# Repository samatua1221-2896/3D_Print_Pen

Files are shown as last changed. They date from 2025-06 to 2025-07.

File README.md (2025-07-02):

# 3D_Print_Pen

This is a fully custom 3D print pen that is able to use standard 1.75 filament and work with temperatures of 130°C to 240°C

fullModel

## Features

- Uses an Arduino Nano to control heating and motor functions
- Temperature dial lets you adjust the nozzle from 130 °C to 240 °C
- PID-controlled heater ensures smooth, stable temperature during use
- 12V 40W MK8-style heater cartridge melts standard 1.75 mm filament
- Compact custom PCB designed in KiCad
- Extrude button: hold to feed, double-tap for continuous release, tap again to stop
- Retract button: same controls in reverse for removing filament
- Motor direction and latching fully handled in firmware with debounce and timing
- Heater auto-shuts off if temp exceeds 260 °C or if thermistor fails
- Failsafe defaults ensure motor and heater are off on startup or error

## Details

This was pretty much my first full dive into a full blast of hardware and software combined in my own project that I'm making from scratch. I got inspiration from the MYNT3D style pen that I had but had been dealt some damage with wear and tear over the years so I decided to try and make my own. Overall, this was a pretty fun project where I was able to get a much better understand of KiCad and Onshape which is definitely going to help me for future projects that I'll be working on. A 3D print pen is also pretty close to a 3D printer that I'm hoping to get but if all else fails I'll have a pretty cool piece of hardware that I'll know I completely designed from scratch.

## Photos

Front & Back Exploded Views

frontExplodedView
backExplodedView

Pictures of PCB Board Front & Back

frontPrintPenPCB
backPrintPenPCB

Schematic Wiring

printPenSchematic

## Assembly Instructions

Most of this is a pretty straightforward setup with the PCB board being the main center of the pen that has all of the THT components sticking out of the case in order or operation to happen. If it is not defined inside of the 3D model how something is secured, the object is glued to the nearest surrounding case area. For example, the hotend nozzle will be glued to the innermost cylinder in order to minimize the amount of screws and scructural instability inside of the case itself.

## Side Notes

I do understand the preference of getting supplies from places like AliExpress, but unfortunately, living in Hawaii removes a lot of the options that are even availble on such websites. The best option for getting things to Hawaii in time for the Highway event is unfortunately going to need increased shipping. (Just for context, the PCB I ordered at the beginning on June still hasn't arrived yet) That means that some items in my BOM are a little pricier that AliExpress or otherwise counterparts but they are guaranteed able to arrive on time for the end of the event.

## Bill Of Materials

| Item |  Quantity | Price | Link |
|---|---|---|---|
| Arduino Nano | 3 | $7.99 | https://www.amazon.com/YELUFT-ATmega328P-Microcontroller-Mini-USB/dp/B0DWMQVCRF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 |
| IRLZ44N MOSFET | 1 | $1.30 | https://www.digikey.com/en/products/detail/infineon-technologies/IRLZ44NPBF/811808 |
| L293D Motor Driver IC | 1 | $7.85 | https://www.digikey.com/en/products/detail/stmicroelectronics/L293D/634700 |
| 10K Potentiometer (Vertical Mount) | 1 | $0.78 | https://www.digikey.com/en/products/detail/amphenol-piher-sensing-systems/PT10WV10-103A2020-3-NE-S/13244529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 |
| MK8 Hotend Heating Kit | 1 | $17.35 | https://www.amazon.com/KITQLPG-Assembled-Extruder-Aluminum-Creality/dp/B0DM1XC4MV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 |
| 12V 2A Power Adapter | 1 | $0.00 | N/A |
| 220 Ohm Resistor | 1 | $0.10 | https://www.digikey.com/en/products/detail/vishay-beyschlag-draloric-bc-components/MBA02040C2203FRP00/336479 |
| 10K Ohm Resistor | 2 | $0.20 | https://www.digikey.com/en/products/detail/stackpole-electronics-inc/RNF14FTD1K00/1706678 |
| 100uF 16V Electrolytic Capacitor | 2 | $0.24 | https://www.digikey.com/en/products/detail/w%C3%BCrth-elektronik/860020372006/5727030 |
| 0.1uF Ceramic Capacitor | 2 | $0.44 | https://www.digikey.com/en/products/detail/kemet/C320C104K5R5TA/818040 |
| 100K NTC Thermsistor EPCOS | 1 | $0.82 | https://www.digikey.com/en/products/detail/epcos-tdk-electronics/B57891M0104J000/739908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 |
| Mini DC Motor 12 V | 1 | $7.31 | https://www.amazon.com/Motor-DC12V-11RPM-Right-Printing/dp/B0B82JPGRB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 |
| Terminal Block 2-pin 3.5mm | 2 | $0.72 | https://www.digikey.com/en/products/detail/w%C3%BCrth-elektronik/691137710002/6644051 |
| Pin Header 1x2 2.54 | 1 | $0.10 | https://www.digikey.com/en/products/detail/harwin-inc/M20-9990246/3728226 |
| M3 Screws | 12 | $5.89 | https://www.digikey.com/en/products/detail/apm-hexseal/RM3X10MM-2701/3712296 |
| 18 AWG Wire | 1 | $6.99 | https://www.amazon.com/Automotive-Flexible-Security-Stranded-Electrical/dp/B0CKR35SX5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 |
| 22 AWG Wire | 1 | $8.98 | https://www.amazon.com/Electrical-Gauge-Silicone-Cable-Black/dp/B0746HG158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 |
| Buttons | 2 | $2.74 | https://www.digikey.com/en/products/detail/c-k/D6C90-F2-LFS/1466345 |
| Shipping for DigiKey | 1 | $20.00 | N/A |
| Shipping for Printing Legion | 1 | $10.00 | N/A |
| DC Barrel Jack | 1 | $1.50 | https://www.digikey.com/en/products/detail/same-sky-formerly-cui-devices/PJ-202AH/408450 |
| PCB Board | 1 | $15.28 | JLCPCB  |
| | | | |
| Total Cost | | $119.32 | |

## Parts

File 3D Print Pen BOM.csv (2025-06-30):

Actual Item Name & Use | Quantity | Order | Cost | Notes | Link to Buy | Status | Order date
Arduino Nano | 3 | 1pcs Nano V3.0 Board with Cable ATmega328P MCU CH340G Chip 5V 16M Microcontroller Compatible with Arduino Nano (Soldered, Type-C Port) | $7.99 |  | https://www.amazon.com/YELUFT-ATmega328P-Microcontroller-Mini-USB/dp/B0DWMQVCRF?s=industrial | Approved
IRLZ44N MOSFET | 1 | IRLZ44NPBF | $1.30 |  | https://www.digikey.com/en/products/detail/infineon-technologies/IRLZ44NPBF/811808 | Approved
L293D Motor Driver IC | 1 | L293D | $7.85 |  | https://www.digikey.com/en/products/detail/stmicroelectronics/L293D/634700 | Approved
10K Potentiometer (Vertical Mount) | 1 | PT10WV10-103A2020-3-NE-S | $0.78 |  | https://www.digikey.com/en/products/detail/amphenol-piher-sensing-systems/PT10WV10-103A2020-3-NE-S/13244529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 | Approved
MK8 Hotend Heating Kit | 1 | 1 Pcs 3D Printer Part 12V 24V Assembled Extruder Hotend Kit MK8 Nozzle Aluminum Heat Block/Fit for Creality Ender-3/CR-10/CR-10 Pro(for CR10 Pro 24V) | $17.35 |  | https://www.amazon.com/KITQLPG-Assembled-Extruder-Aluminum-Creality/dp/B0DM1XC4MV?s=industrial | Approved
12V 2A Power Adapter | 1 | N/A | $0.00 | Already Own | N/A | Delivered
220 Ohm Resistor | 1 | MBA02040C2203FRP00 | $0.10 |  | https://www.digikey.com/en/products/detail/vishay-beyschlag-draloric-bc-components/MBA02040C2203FRP00/336479 | Approved
10K Resistor | 2 | RNF14FTD1K00 | $0.20 |  | https://www.digikey.com/en/products/detail/stackpole-electronics-inc/RNF14FTD1K00/1706678 | Approved
100µF 16V Electrolytic Capacitor | 2 | 860020372006 | $0.24 |  | https://www.digikey.com/en/products/detail/w%C3%BCrth-elektronik/860020372006/5727030 | Approved
0.1µF Ceramic Capacitor | 2 | C320C104K5R5TA | $0.44 |  | https://www.digikey.com/en/products/detail/kemet/C320C104K5R5TA/818040 | Approved
100K NTC Thermistor EPCOS | 1 | B57891M0104J000 | $0.82 |  | https://www.digikey.com/en/products/detail/epcos-tdk-electronics/B57891M0104J000/739908 | Approved
Mini DC Motor 6V-12V | 1 | Gear Motor, DC12V 11RPM N20 Right Angle Metal Micro Gear Motor Low Speed Low Noise Brush DC Motor for 3D Printing Pen | $7.31 |  | https://www.amazon.com/Motor-DC12V-11RPM-Right-Printing/dp/B0B82JPGRB?s=industrial | Approved
Terminal Block 2-pin 3.5mm | 2 | 691137710002 | $0.72 |  | https://www.digikey.com/en/products/detail/w%C3%BCrth-elektronik/691137710002/6644051 | Approved
Pin Header 1x2 2.54mm | 1 | M20-9990246 | $0.10 |  | https://www.digikey.com/en/products/detail/harwin-inc/M20-9990246/3728226 | Approved
M3 Screws | 12 | RM3X10MM 2701 | $5.89 |  | https://www.digikey.com/en/products/detail/apm-hexseal/RM3X10MM-2701/3712296 | Approved
18 AWG Wire | 1 | 18 Gauge Wire (2-Pack Red/Black Each 25 FT), 18 AWG Automotive Wire, CCA, Speaker Audio Cable, Flexible Low Voltage Security Alarm Hook Up Control Cable, Stranded Electrical Wires for DIY DC | $6.99 |  | https://www.amazon.com/Automotive-Flexible-Security-Stranded-Electrical/dp/B0CKR35SX5?s=industrial | Approved
22 AWG Wire | 1 | 22awg Silicone Electrical Wire Cable 6 Colors (10ft Each) 22 Gauge Hookup Wires kit Stranded Tinned Copper Wire Flexible and Soft | $8.98 |  | https://www.amazon.com/Electrical-Gauge-Silicone-Cable-Black/dp/B0746HG158?s=industrial | Approved
Buttons | 2 | D6C90 F2 LFS | $2.74 |  | https://www.digikey.com/en/products/detail/c-k/D6C90-F2-LFS/1466345 | Approved
Shipping for DigiKey | 1 | N/A | $20.00 |  | N/A | Approved
Shipping for PETG 3D Print Parts | 1 | N/A | $10.00 |  | N/A | Approved
DC Barrel Jack (Female, PCB Mount) | 1 | PJ-202AH | $1.50 |  | https://www.digikey.com/en/products/detail/same-sky-formerly-cui-devices/PJ-202AH/408450 | Approved
PCB | 1 | PCB | $15.28 | Projected Cost, May Increase w/ Shipping | JLCPCB
 |  |  | $119.32

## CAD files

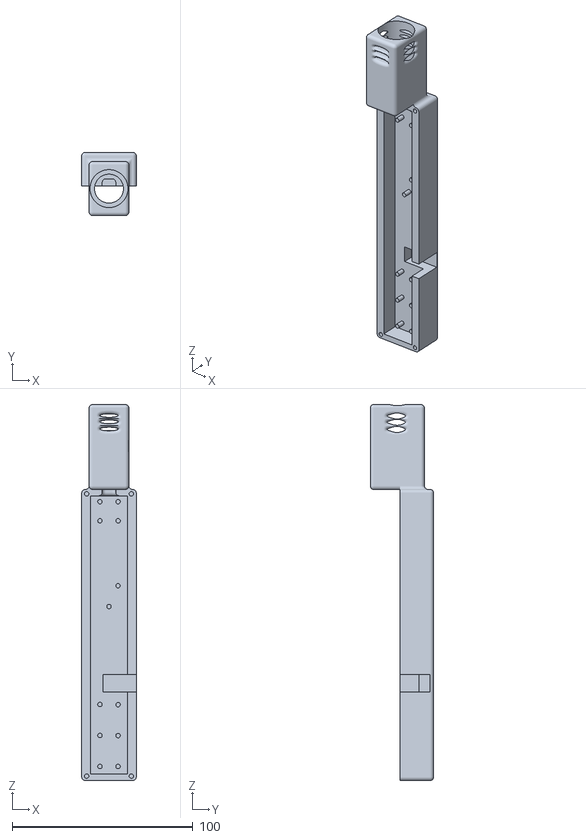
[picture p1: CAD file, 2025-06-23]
CAD/Main Case.stl
30.2 x 35.1 x 208.0

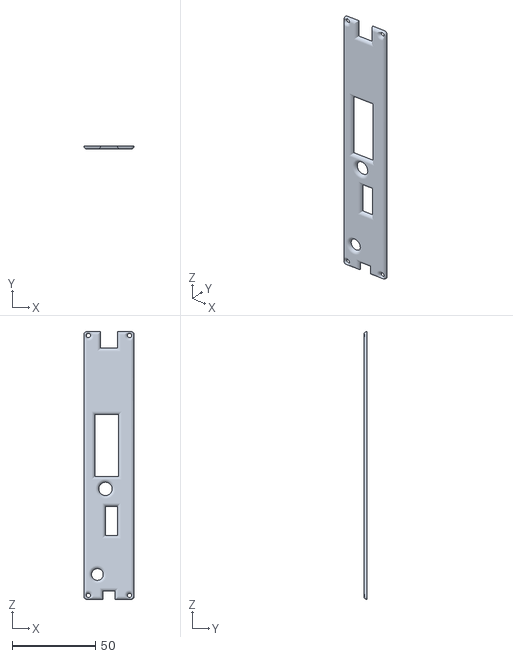
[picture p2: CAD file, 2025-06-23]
CAD/Top Case.stl
30.2 x 2.00 x 161.0

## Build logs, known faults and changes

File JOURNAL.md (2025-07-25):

| Title | Author | Description | Date Started |
| --- | --- | --- | ---|
| Arm Assistant | @samatua1221-2896 | A custom 3D printing pen | 6/18/25 |

### Overall Time Spent Designing as of July 1: 35 hrs

# June 18, 2025 (7 hours)

Today I decided I wanted to try and make a custom 3D printing pen that's pretty simple in terms of its ability but also has basic functionality. (I also really want some type of 3D printing tool like a 3D printer from highway maybe...) I started to base the concept off of MYNT3D's pen, it took me a little while but I was actually able to break it apart and figure out how the entire thing worked.

Based on the pictures below, I figured out that the pen had a potentiometer to adjust the temperature settings, there were two buttons to control the extruding and retraction of the filament, there was a slider to adjust the speed, and a small DC motor to actually control the movement of the filament. I decided I wanted to basically keep the basic functionality of the MYNT3D pen but have my own spin on it. I did want the entire thing to be powered by a 12V barrel jack to keep it simple. The microcontroller that was inside the MYNT pen looked to be some type of custom-made object, so I decided to use an Arduino Nano to keep it pretty simple for me so far.




So far I've been working on the schematic that I can use, I eventually settled on keeping the manual potentiometer instead of a LCD screen, aside from that, I've just been working to keep the whole thing pretty simple and not too complex in its parts, also using THT components cause I've never had experience working with surface mounted components. Below is the main schematic that I have so far for it.

Screenshot 2025-06-18 5 01 48 PM

Tomorrow I'll work on arranging the PCB and starting to work on the CAD and wiring structure for the pen.

# June 19, 2025 (8 hrs)

Today I worked on getting my BOM in order and finishing up the design of my PCB. So far, it's looking like theres not too much to do. I did start working on my BOM and figuring out how to get the products, I started using AliExpress and was extrememly happy to find that almost everything I needed was super cheap and not a problem to find at all. Then I went to go check out and found that none of them ship to Hawaii (:( whyyyy tarrifs) so it looks like I'm going to be searching on Amazon for the best prices again even if that means a little bit of a cost raise. 

Aside from that, now it looks like I've finished my PCB and it's not looking to bad if I say so myself. The pieces are relatively simple to fix and put on so I think it's looking pretty good so far.

Screenshot 2025-06-19 11 49 11 PM

I did spend quite a bit of time trying to fix all the rails, but pretty much I think this should be the final version of my PCB. Im planning on having the buttons on top and the power and potentiometer coming out of the back just to avoid having some things at awkward positions while I'm using the pen. 

# June 20, 2025 

I spend A LOT of time trying to finalize my BOM today so I can start working on the CAD to place everything. I did start with Amazon thinking I wouldn't be able to afford shipping from anywhere else when I happened to stumble on DigiKey! Thank god they're US based so there's not going to be too many charges aside from regular shipping to Hawaii. Majority of the parts that I'm going to need are just going to be soldered though-hole on my PCB since it's easier for my project. I am keeping some of the parts on Amazon just because I feel like those should be higher quality items that are vetted more for my project so hopefully that's ok. I did end up picking a nozzle from what an Ender 3D printer would be using because I didn't want my project to be your run-of-the-mill 3D pen, I did want to try and be a little more creative so I wanted to try and play around with that type of heat tip.

So far this is what I have in my BOM, it's pretty messy but I think I should be able to clean it up pretty nicely over the next two days. For me personally, I'm trying to finish this project BEFORE July so I can eventually get enough points for that 3D printer.

# June 21, 2025 (10 hrs - last 2 days)

I actually did end up having a much harder time dealing with the actual PCB design of the baord once I realized that my tracks were probabaly too thin for the amount of power that I was trying to use. After plenty of time trying to figure out how to asign net classes to all of my parts, I eventually was able to wire everything up and after even MORE time I was able to manuever all of my wiring around the thicker lines. 

Screenshot 2025-06-21 8 05 26 PM
Screenshot 2025-06-21 8 05 56 PM

I did stop my journal a little early yesterday because of one of my brother's basketball games, but I did end up figuring out all of my BOM materials. So far, it's looking like it'll be around $100, well under the grant limit for my project I hope (fingers crossed!) Listed below is my current BOM that hopefully wont change much more since I'll start working on the CAD now. Majority of my supplies are going to be sourced from Digikey with "higher quality" items coming from Amazon.

Screenshot 2025-06-21 8 35 13 PM

Now I'm going to start making mockups for the whole 3D pen in Onshape, hopefully it won't take too long.

# June 22, 2025 (5 hrs)

So that actually took a LOT longer than I thought it would take. I'm realizing now that a lot of the components are bigger than I previously thought they would be so I'm going to try and shift around the design a little bit to try and mae sure that I can keep what I have so far which is there below.

Screenshot 2025-06-22 1 20 25 AM

# June 28, 2025 (3 hrs)

It's been a while since I've been able to work on the project, but now it loks like that it should be wrapping up now. CAD is now I belive completely finished with so now I have a complete plan for where everything will go and how it will all work. I did have to change a couple of things due to the size of the nozzle. I was planning on having everything to do with the nozzle be wrapped inside of the case but I don't believe I'm skilled in CAD enough to know how to do it in a way that would protect the PCB and be physically stable. I did add a couple of things like ventilation holes on the side of the nozzle and shifted around the placement of the motor that will carry the filament. Aside from that, just minor things like smoothing out all the edges and making sure all my parts are the correct ones are pretty much all I have left for CAD. Soon I'll start on writing the code for it but it should be a pretty simple task.

Screenshot 2025-06-28 7 53 55 PM
Screenshot 2025-06-28 7 54 03 PM
Screenshot 2025-06-28 7 45 57 PM

Ok, I just finished writing up the code with a good amount of help from ChatGPT since I'm not super experienced in it but I do believe that I am now finished and now I'm going to be working on the README and the submission files, crossing fingers for a good result!

# July 1, 2025 (2 hrs)

Today I really just spent time working on the README file and doing the finishing touches on all of my CAD files and labeling. Hopefully the project looks good and I'm going on the submission now, so wish me luck!

# July 24, 2025

Finally got my grant and some of the parts started to arrive today, going to wait until tomorrow to start soldering everything together so I can get the rest of my packages coming from Amazon.

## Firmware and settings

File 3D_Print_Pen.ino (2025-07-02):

/* -----------------------------------------------------------------
   DIY 3‑D Printing Pen – Full Firmware
   Hardware (per KiCad project):
     * Arduino Nano V3 / Nano Every
     * L293D (IN1 = D2, IN2 = D3, EN1/2 tied HIGH or PWM for speed)
     * IRLZ44N MOSFET gate on D9  (Heater PWM)
     * Extrude button  on D4   (to GND, INPUT_PULLUP)
     * Retract button  on D5   (to GND, INPUT_PULLUP)
     * Potentiometer   on A1   (10 kΩ, sets 130‑240 °C)
     * Thermistor      on A0   (100 kΩ NTC, β ~ 3950, 10 kΩ pull‑up to 5 V)
------------------------------------------------------------------- */

#include <Arduino.h>

/* ---------- PIN DEFINITIONS ---------- */
constexpr uint8_t PIN_IN1       = 2;    // L293D IN1 (Motor FWD)
constexpr uint8_t PIN_IN2       = 3;    // L293D IN2 (Motor REV)
constexpr uint8_t PIN_BTN_FWD   = 4;    // Extrude button
constexpr uint8_t PIN_BTN_REV   = 5;    // Retract button
constexpr uint8_t PIN_HEATER    = 9;    // MOSFET gate PWM
constexpr uint8_t PIN_THERMIST  = A0;   // Thermistor
constexpr uint8_t PIN_POT       = A1;   // Temp set potentiometer

/* ---------- CONSTANTS ---------- */
const float    BETA        = 3950.0;    // β constant of thermistor
const float    T0          = 298.15;    // 25 °C in Kelvin
const float    R0          = 100000.0;  // 100 kΩ at 25 °C
const float    PULLUP      = 10000.0;   // 10 kΩ pull‑up resistor
const uint16_t ADC_MAX     = 1023;
const float    VREF        = 5.0;       // ADC reference voltage

const uint16_t TEMP_MIN_C  = 130;       // lower limit of set‑pot range
const uint16_t TEMP_MAX_C  = 240;       // upper limit

/* PID tuning (start values, adjust by experiment) */
float Kp = 10.0;
float Ki = 0.6;
float Kd = 50.0;

/* Button timing  */
const unsigned long DEBOUNCE_MS = 25;
const unsigned long DOUBLE_MS   = 400;

const uint16_t TEMP_MAX_SAFE = 260;   // °C, heater shutdown threshold

enum MotorState { STOPPED, FORWARD, REVERSE };

struct Btn {
  uint8_t  pin;
  bool     lastLevel;
  bool     isDown;
  unsigned long lastChange;
  unsigned long firstClick;
  bool     latched;
};

/* ---------- GLOBALS ---------- */
Btn btnFwd = {PIN_BTN_FWD, HIGH, false, 0, 0, false};
Btn btnRev = {PIN_BTN_REV, HIGH, false, 0, 0, false};

MotorState motorState = STOPPED;

float tempSetC  = 0;
float tempNowC  = 0;

/* PID terms */
float pidIntegral = 0;
float pidPrevErr  = 0;
unsigned long lastPIDms = 0;
const unsigned long PID_INTERVAL_MS = 200;

float readTemperatureC();
void  updatePID();
void  setHeaterPWM(uint8_t duty);
void  setMotor(MotorState st);
void  handleButton(Btn &b, MotorState dir);

void setup() {
  pinMode(PIN_IN1, OUTPUT);
  pinMode(PIN_IN2, OUTPUT);
  pinMode(PIN_HEATER, OUTPUT);

  pinMode(PIN_BTN_FWD, INPUT_PULLUP);
  pinMode(PIN_BTN_REV, INPUT_PULLUP);

  /* Safe defaults */
  setMotor(STOPPED);
  setHeaterPWM(0);

#ifdef SERIAL_PORT_USBVIRTUAL
  Serial.begin(115200);
#endif
}

void loop() {

  handleButton(btnFwd, FORWARD);
  handleButton(btnRev, REVERSE);

  int potRaw = analogRead(PIN_POT);
  tempSetC = map(potRaw, 0, ADC_MAX, TEMP_MIN_C, TEMP_MAX_C);

  tempNowC = readTemperatureC();

  if (tempNowC > TEMP_MAX_SAFE || tempNowC < 0) {
    // Sensor failure or runaway
    setHeaterPWM(0);
  } else {

     unsigned long now = millis();
    if (now - lastPIDms >= PID_INTERVAL_MS) {
      updatePID();
      lastPIDms = now;
    }
  }

#ifdef SERIAL_PORT_USBVIRTUAL
  static unsigned long lastPrint = 0;
  if (millis() - lastPrint > 1000) {
    Serial.print("Set:"); Serial.print(tempSetC);
    Serial.print("  Now:"); Serial.print(tempNowC);
    Serial.print("  Motor:"); Serial.println(motorState);
    lastPrint = millis();
  }
#endif
}


void handleButton(Btn &b, MotorState dir) {
  bool level = digitalRead(b.pin);
  unsigned long now = millis();

  /* Debounce */
  if (level != b.lastLevel) {
    b.lastChange = now;
    b.lastLevel  = level;
  }
  if (now - b.lastChange < DEBOUNCE_MS) return;

  if (!level && !b.isDown) {
    b.isDown = true;
    if (now - b.firstClick < DOUBLE_MS) {          // Double click
      b.latched = !b.latched;                      // Continuous
      if (b.latched) setMotor(dir);
      else           setMotor(STOPPED);
      b.firstClick = 0;
    } else {
      b.firstClick = now;                          // Start click timer
    }
  }

  /* On release */
  if (level && b.isDown) {
    b.isDown = false;
    if (!b.latched && (now - b.firstClick >= DOUBLE_MS)) {
      setMotor(STOPPED);                           // End of momentary
    } else if (b.latched) {                        // Single click stops latched
      b.latched = false;
      setMotor(STOPPED);
    }
  }

  /* Momentary running while held */
  if (b.isDown && !b.latched) setMotor(dir);
}


void setMotor(MotorState st) {
  motorState = st;
  switch (st) {
    case FORWARD:
      digitalWrite(PIN_IN1, HIGH);
      digitalWrite(PIN_IN2, LOW);
      break;
    case REVERSE:
      digitalWrite(PIN_IN1, LOW);
      digitalWrite(PIN_IN2, HIGH);
      break;
    case STOPPED:
    default:
      digitalWrite(PIN_IN1, LOW);
      digitalWrite(PIN_IN2, LOW);
  }
}



void updatePID() {
  float err = tempSetC - tempNowC;
  pidIntegral += err * (PID_INTERVAL_MS / 1000.0);
  float derivative = (err - pidPrevErr) / (PID_INTERVAL_MS / 1000.0);
  float out = Kp * err + Ki * pidIntegral + Kd * derivative;

  /* Clamp and write PWM */
  out = constrain(out, 0, 255);
  setHeaterPWM((uint8_t)out);
  pidPrevErr = err;
}

void setHeaterPWM(uint8_t duty) {
  analogWrite(PIN_HEATER, duty);
}

/* ====================================================
   THERMISTOR CONVERSION
==================================================== */
float readTemperatureC() {
  int raw = analogRead(PIN_THERMIST);
  if (raw <= 0 || raw >= ADC_MAX) return -100.0;   // Detect open/short

  float v = (raw * VREF) / ADC_MAX;
  float rTherm = PULLUP * ( (VREF / v) - 1.0 );
  if (rTherm <= 0) return -100.0;
  float invT = 1.0/T0 + (1.0/BETA) * log(rTherm / R0);
  float tempK = 1.0 / invT;
  float tempC = tempK - 273.15;
  return tempC;
}

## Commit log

2025-06-29 Rename 3D_Print_Pen-B_Cu.gbr to PCB Files/3D_Print_Pen-B_Cu.gbr
    [3D_Print_Pen-B_Cu.gbr]
2025-06-29 Rename 3D_Print_Pen-B_Mask.gbr to PCB Files/3D_Print_Pen-B_Mask.gbr
    [3D_Print_Pen-B_Mask.gbr]
2025-06-29 Rename 3D_Print_Pen-B_Silkscreen.gbr to PCB Files/3D_Print_Pen-B_Silkscreen.gbr
    [3D_Print_Pen-B_Silkscreen.gbr]
2025-06-29 Rename 3D_Print_Pen-F_Cu.gbr to PCB Files/3D_Print_Pen-F_Cu.gbr
    [3D_Print_Pen-F_Cu.gbr]
2025-06-29 Rename 3D_Print_Pen-F_Mask.gbr to PCB Files/3D_Print_Pen-F_Mask.gbr
    [3D_Print_Pen-F_Mask.gbr]
2025-06-29 Rename 3D_Print_Pen-F_Silkscreen.gbr to PCB Files/3D_Print_Pen-F_Silkscreen.gbr
    [3D_Print_Pen-F_Silkscreen.gbr]
2025-06-29 Rename 3D_Print_Pen-PTH.drl to PCB Files/3D_Print_Pen-PTH.drl
    [3D_Print_Pen-PTH.drl]
2025-06-29 Rename 3D_Print_Pen-job.gbrjob to PCB Files/3D_Print_Pen-job.gbrjob
    [3D_Print_Pen-job.gbrjob]
2025-06-29 Rename Archive.zip to PCB Files/Archive.zip
2025-06-30 Update 3D Print Pen BOM.csv
    [3D Print Pen BOM.csv]
2025-07-03 Rename Main Assembly.step to Full 3D Model.step
    [Full 3D Model.step]
